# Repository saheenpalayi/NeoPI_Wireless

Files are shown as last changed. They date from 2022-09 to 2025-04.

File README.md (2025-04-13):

# Neoπ Wireless CNC Controller (3-axis) 
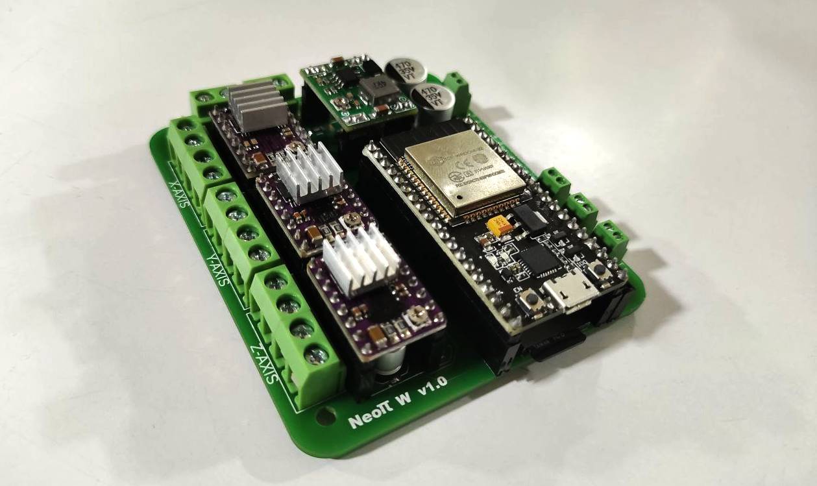
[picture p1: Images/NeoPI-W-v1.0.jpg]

## Project Overview
This project was made for ESP32 based 3-Axis Milling Machines. I started this project During my time at the FAB LAB Kerala for an awesome project Called [FAB Neo](https://fab.cba.mit.edu/classes/865.21/people/rahul/) by Rahul s Rajan. He was developing an Open source fully compact easy to Use PCB Milling Machine Over the years.

## Fetures of Neoπ Wireless CNC Controller
- NodeMCU-32 ESP32 38 Pin  Board based Controller
- SD Card Supported
- A4988/DRV8825 and SPI TMC 2130 stepper Drivers supported
- Reverse Polarity Protection
- Over Voltage protection**
- 12v/24 compatible
- OTA Supports
- PWM Spindle Support
- 2 Probes available (PROB1 and PROB2)
- Power LED Indications RED(power) and Green (5V)

** Optional The board works even without this feature.

## Hardware Pin Mapping

| Sl No | Pin-Names | GPIO |
| --- | --- | --- |
| 1 | X_Dir | GPIO26 |
| 2 | X_Step | GPIO12 |
| 3 | Y_Dir | GPIO25 |
| 4 | Y_Step | GPIO14 |
| 5 | Z_Dir | GPIO33 |
| 6 | Z_Step | GPIO27 |
| 7 | X_limit | GPIO21 |
| 8 | Y_limit | GPIO4 |
| 9 | Z_limit | GPIO15 |
| 10 | Stepper_disable | GPIO13 |
| 11 | Spindle | GPIO17 |
| 12 | PB1 | GPIO32 |
| 13 | PB2 | GPIO22 |

## Firmware

- Use [Grbl_ESP32](https://github.com/bdring/Grbl_Esp32) with [NeoPI_W_v1.h](https://github.com/saheenpalayi/NeoPI_Wireless/blob/main/Firmware/NeoPI_W_v1.h) machine file

## Credits
The Grbl_ESP32 firmware and the ESP32 Hardware is a well-written Open source Project by [bdring](https://github.com/bdring) A K A Barton Dring.

I took reference from these two projects mentioned below
- [Grbl_ESP32_Development_Controller](https://github.com/bdring/Grbl_ESP32_Development_Controller)
- [A 4 axis ESP32 CNC controller for daisy chained SPI stepper drivers](https://github.com/bdring/4_Axis_SPI_CNC#revision-history)
## Revision History
**v1.0**
- version 1 is my first build it has some problems and fixes to do

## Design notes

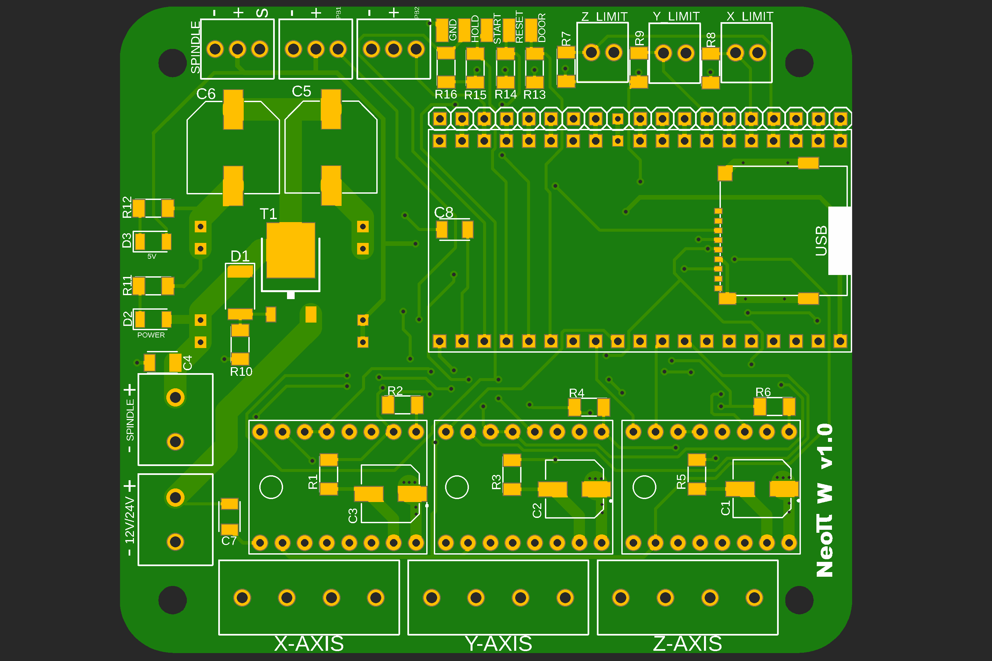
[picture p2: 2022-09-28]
Images/PCB_Top_Side.png

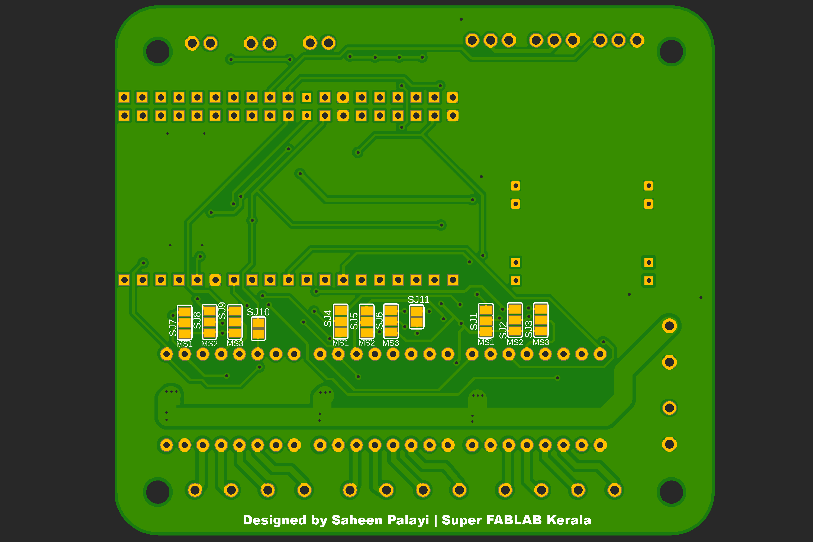
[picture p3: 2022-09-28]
Images/PCB_Bottom_side.png

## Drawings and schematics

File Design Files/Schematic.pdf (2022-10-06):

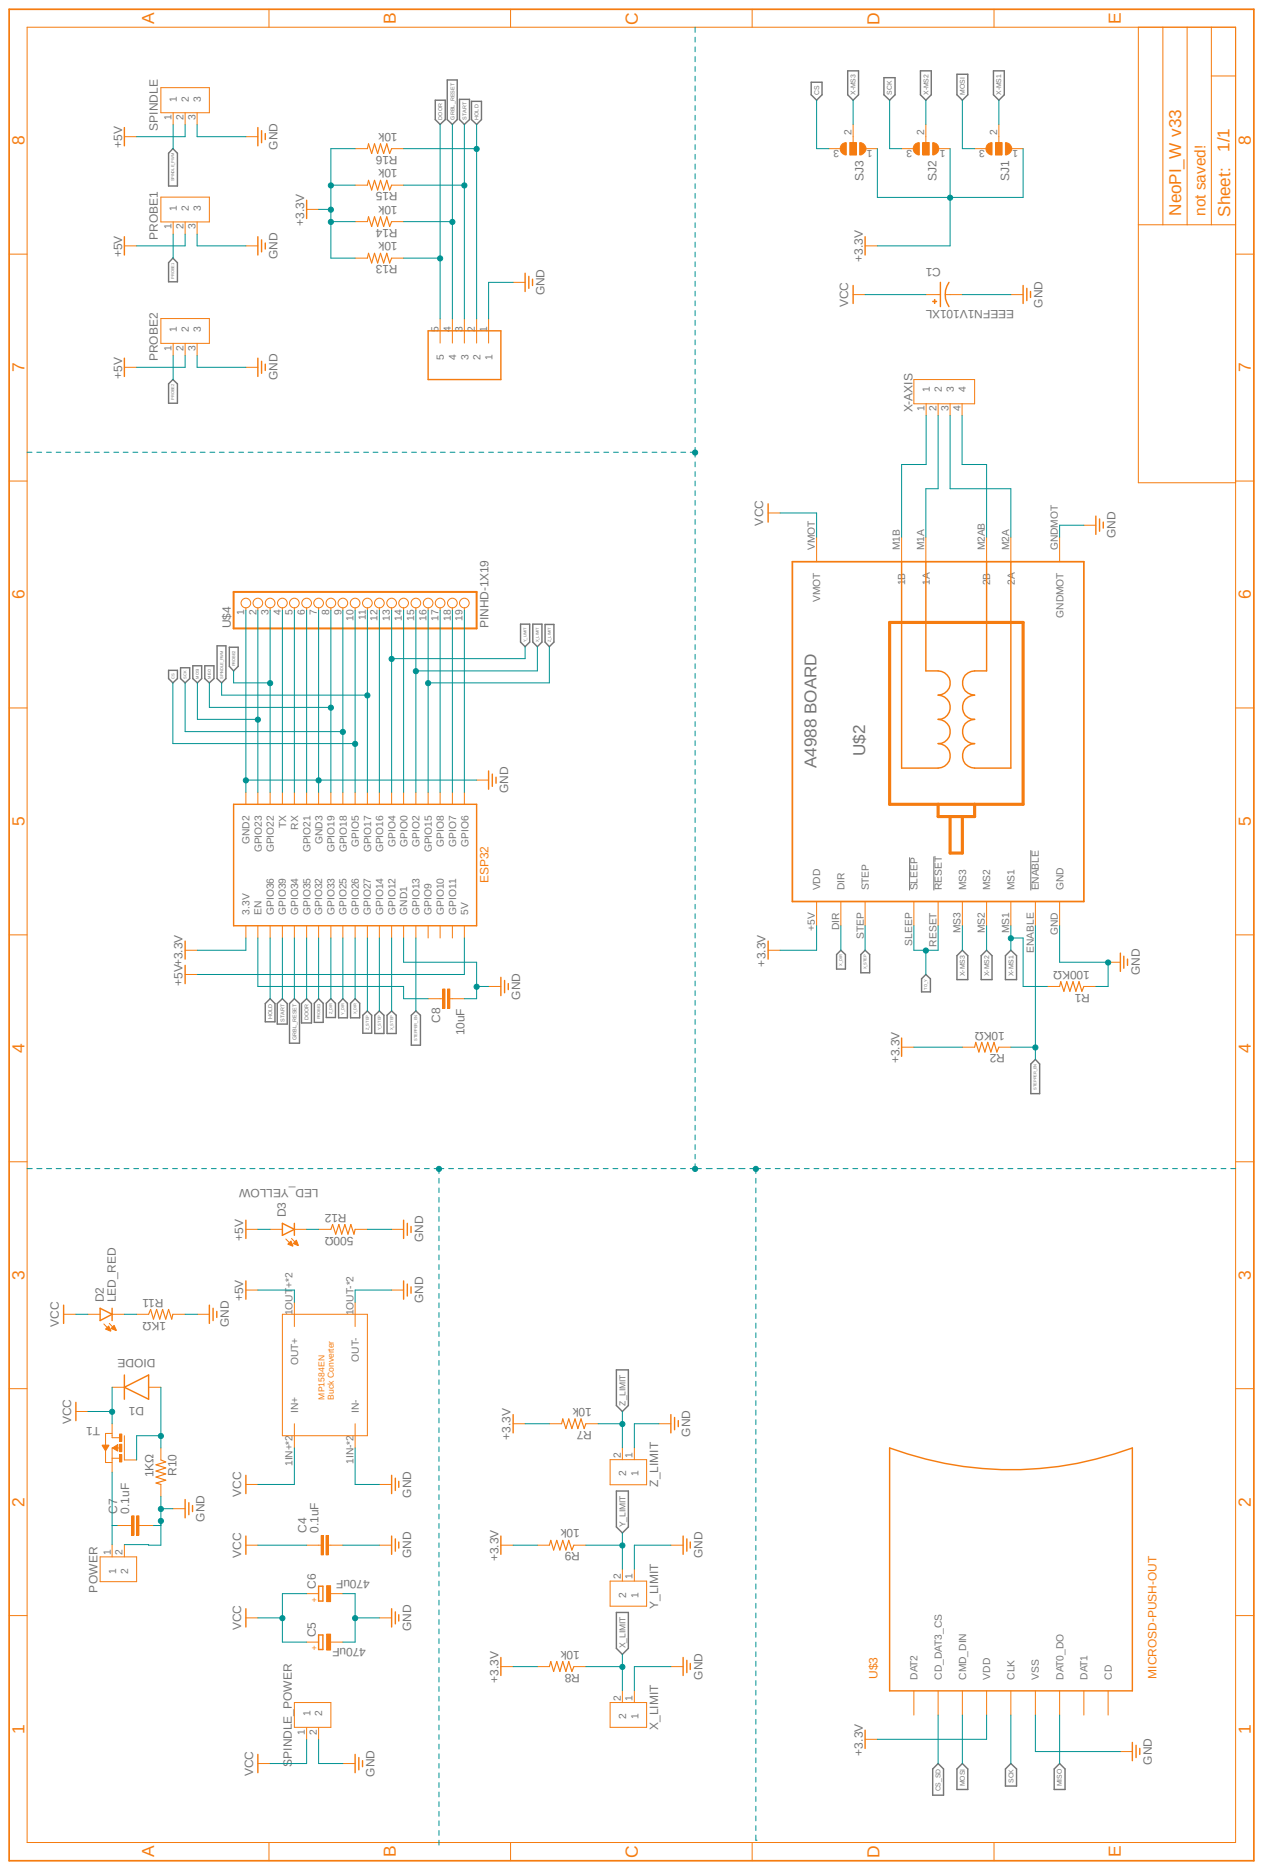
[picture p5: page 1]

C1 IN+ 1IN+*2 IN- 1IN-*2 OUT- 1OUT-*2 OUT+ 1OUT+*2 SPINDLE 1 1 2 2 3 3 X_LIMIT 1 1 2 2 Y_LIMIT 1 1 2 2 Z_LIMIT 1 1 2 2 PROBE1 1 1 2 2 3 3 PROBE2 1 1 2 2 3 3 SPINDLE_POWER 1 1 2 2 POWER 1 1 2 2 C4 R7R8 R9 C5 C6 R10 D1 C7 D2 D3 R11 R12 T1 5 5 4 4 3 3 2 2 1 1 R13 R14 R15 R16 C8 X_STEP X_STEP X_DIR X_DIR TO_Y CS CS SCK SCK SCK MOSI MOSI MOSI MISO MISO CS_SD PROBE2 PROBE2 Z_DIR Z_STEP X-MS3 X-MS3 X-MS2 X-MS2 X-MS1 X-MS1 Y_DIR Y_STEP SPINDLE_PWM SPINDLE_PWM Y_LIMIT Y_LIMIT X_LIMIT X_LIMIT Z_LIMIT Z_LIMIT STEPPER_EN STEPPER_EN PROBE1 PROBE1 HOLD HOLD START START GRBL_RESET GRBL_RESET DOOR DOOR ESP32 U$3 MICROSD-PUSH-OUT MP1584EN Buck Converter ++ NeoPI_W v33 not saved!1/1 Sheet: ABCDE 1 2 3 4 5 6 7 8 ABCDE 1 2 3 4 5 6 7 8

470uF VCC GND GND VCC GND GND GND 1KΩ DIODE0.1uF +5V +5V +5V LED_RED

10k 10k 10k 10k GND +3.3V +3.3V +3.3V10uF 3.3V ENGPIO36 GPIO39 GPIO34 GPIO35 GPIO32 GPIO33 GPIO25 GPIO26 GPIO27 GPIO14 GPIO12 GND1 GPIO13 GPIO9 GPIO10 GPIO11 5V GPIO8 GPIO7 GPIO6 GPIO15 GPIO4 GPIO0 GPIO2 GPIO17 GPIO16 GPIO5 GPIO19 GPIO18 GND3 GPIO21TXRX GPIO23 GPIO22 GND2 U$2 ENABLE ENABLE MS1 MS1 MS2 MS2 MS3 MS3 RESET RESET SLEEP SLEEP STEP STEP DIR DIR VMOT VMOT GNDMOT GNDMOT VDD +5V GND GND 2A M2A 2B M2AB 1A M1A 1B M1B R1 R2 SJ1 3 1 2 SJ2 3 1 2 SJ3 3 1 2 DAT2 CD_DAT3_CS CMD_DIN VDD CLK VSS DAT0_DO DAT1 CD X-AXIS 1 1 2 2 3 3 4 4 U$412345678910111213141516171819

10KΩ +3.3V +3.3V GND +5V+3.3V GND GND PINHD-1X19 VCC

EEEFN1V101XL GND VCC +5V GND GND VCC GND 0.1uF VCC GND

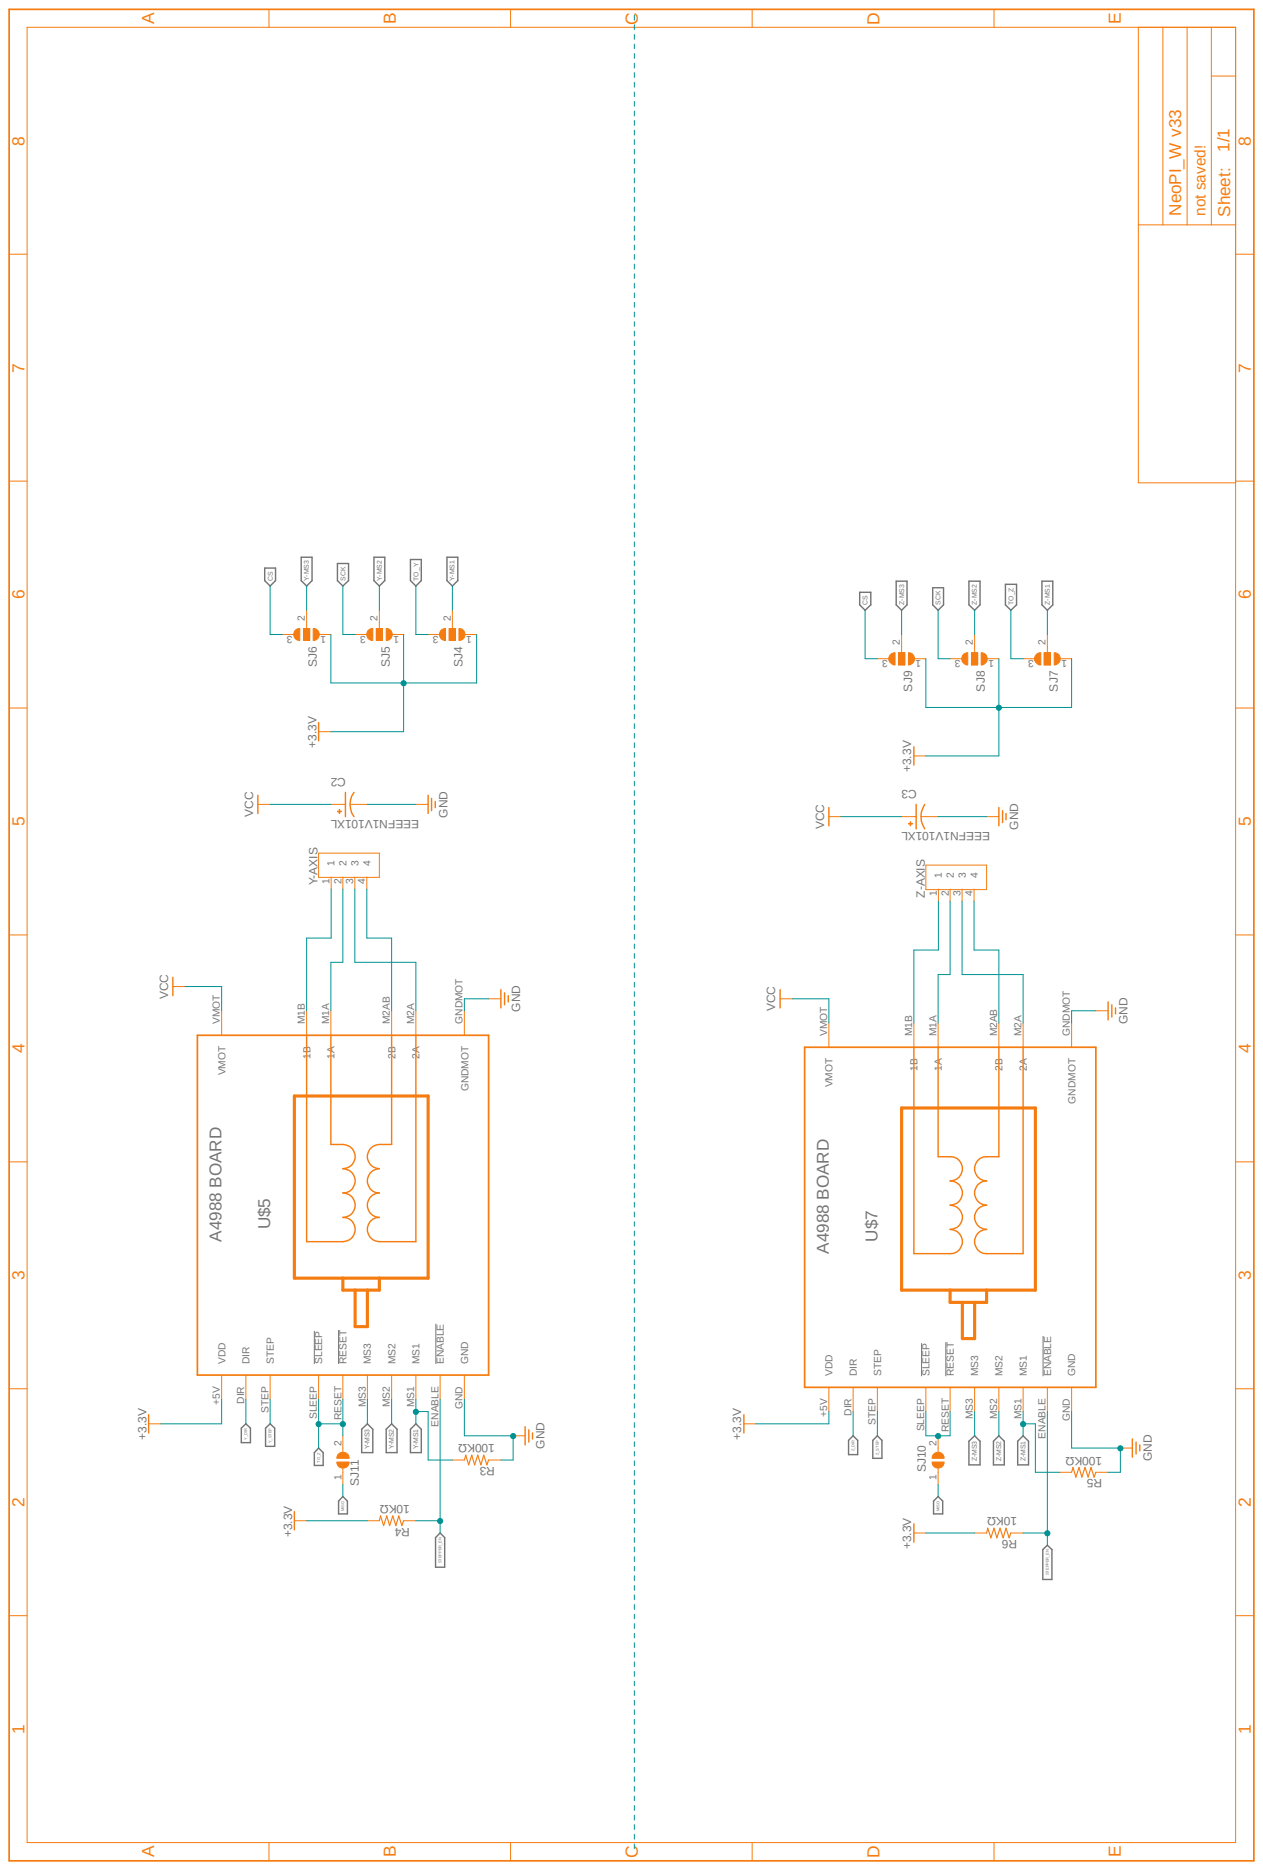
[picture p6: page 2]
10KΩ +3.3V VCC; EEEFN1V101XL GND VCC

C2 C3 SJ102 1SJ11 2 1 CSTO_Y CS SCK SCK MISO MISO TO_Z TO_Z Z_DIR Z_STEP Y-MS3 Y-MS3 Y-MS2 Y-MS2 Y-MS1 Y-MS1 Z-MS3 Z-MS3 Z-MS2 Z-MS2 Z-MS1 Z-MS1 Y_DIR Y_STEP STEPPER_EN STEPPER_EN NeoPI_W v33 not saved!1/1 Sheet: ABCDE 1 2 3 4 5 6 7 8 ABCDE 1 2 3 4 5 6 7 8

EEEFN1V101XL GND +3.3V +3.3V +3.3V +3.3V U$5 ENABLE ENABLE MS1 MS1 MS2 MS2 MS3 MS3 RESET RESET SLEEP SLEEP STEP STEP DIR DIR VMOT VMOT GNDMOT GNDMOT VDD +5V GND GND 2A M2A 2B M2AB 1A M1A 1B M1B R3 R4 SJ4 3 1 2 SJ5 3 1 2 SJ6 3 1 2 Y-AXIS 1 1 2 2 3 3 4 4 U$7 ENABLE ENABLE MS1 MS1 MS2 MS2 MS3 MS3 RESET RESET SLEEP SLEEP STEP STEP DIR DIR VMOT VMOT GNDMOT GNDMOT VDD +5V GND GND 2A M2A 2B M2AB 1A M1A 1B M1B R5 R6 SJ7 3 1 2 SJ8 3 1 2 SJ9 3 1 2 Z-AXIS 1 1 2 2 3 3 4 4

10KΩ +3.3V A4988 BOARD GND GNDVCC

A4988 BOARD GND GNDVCC

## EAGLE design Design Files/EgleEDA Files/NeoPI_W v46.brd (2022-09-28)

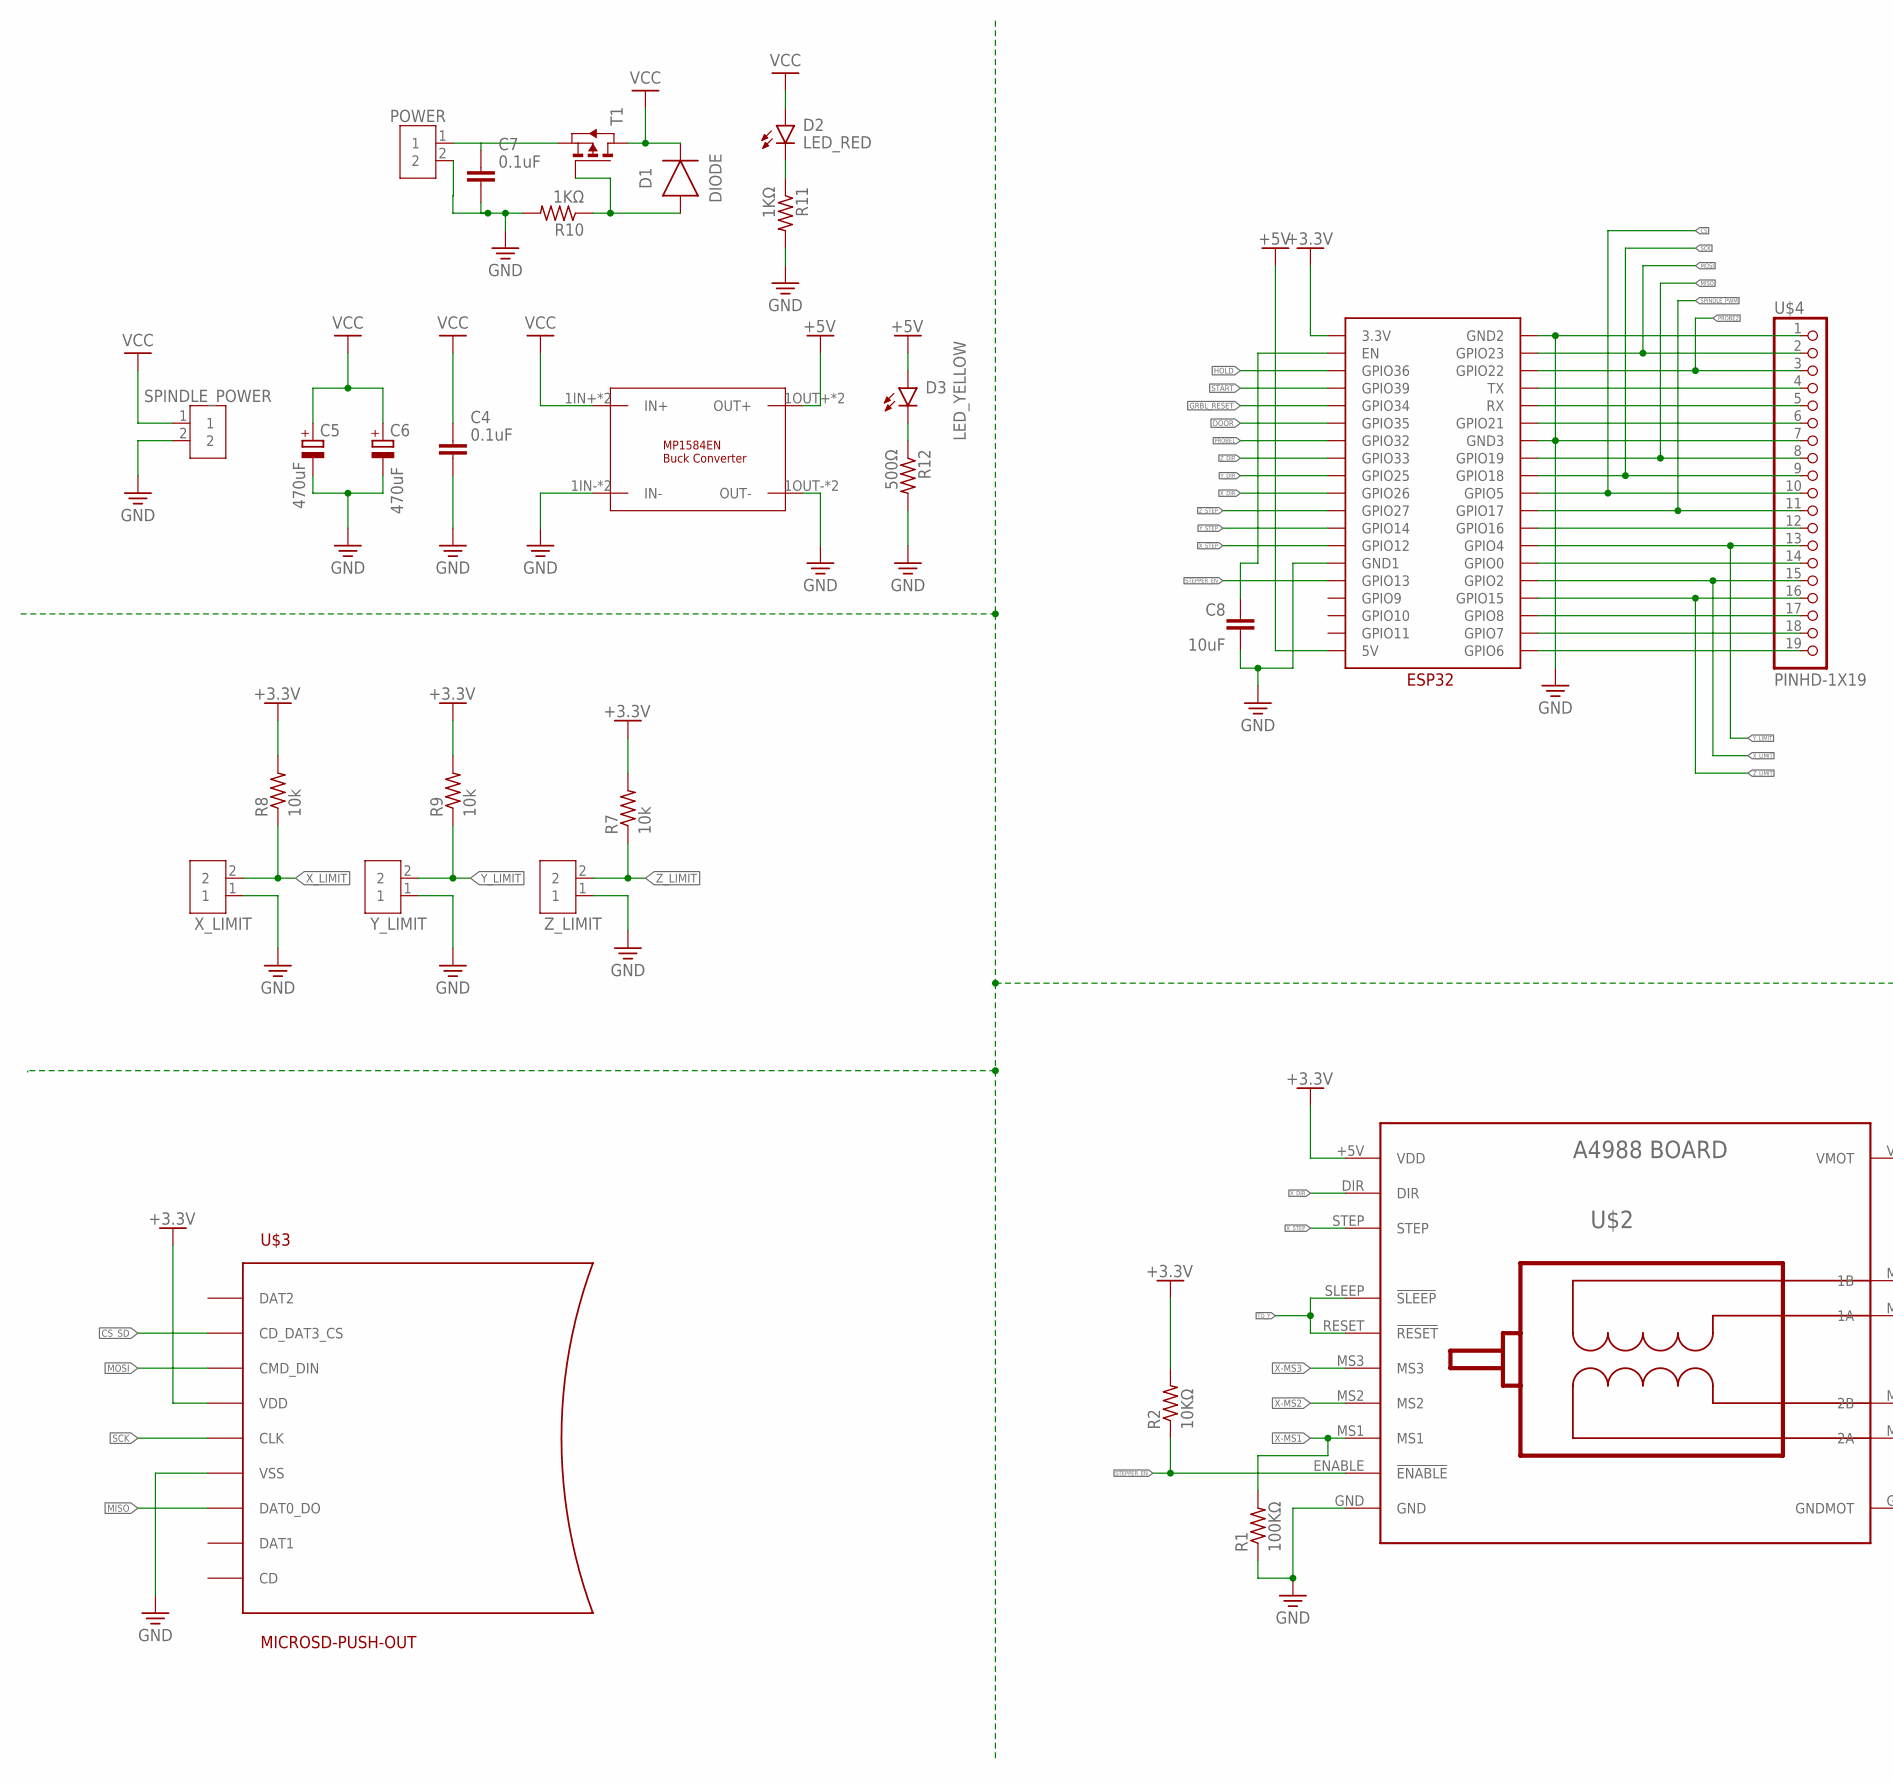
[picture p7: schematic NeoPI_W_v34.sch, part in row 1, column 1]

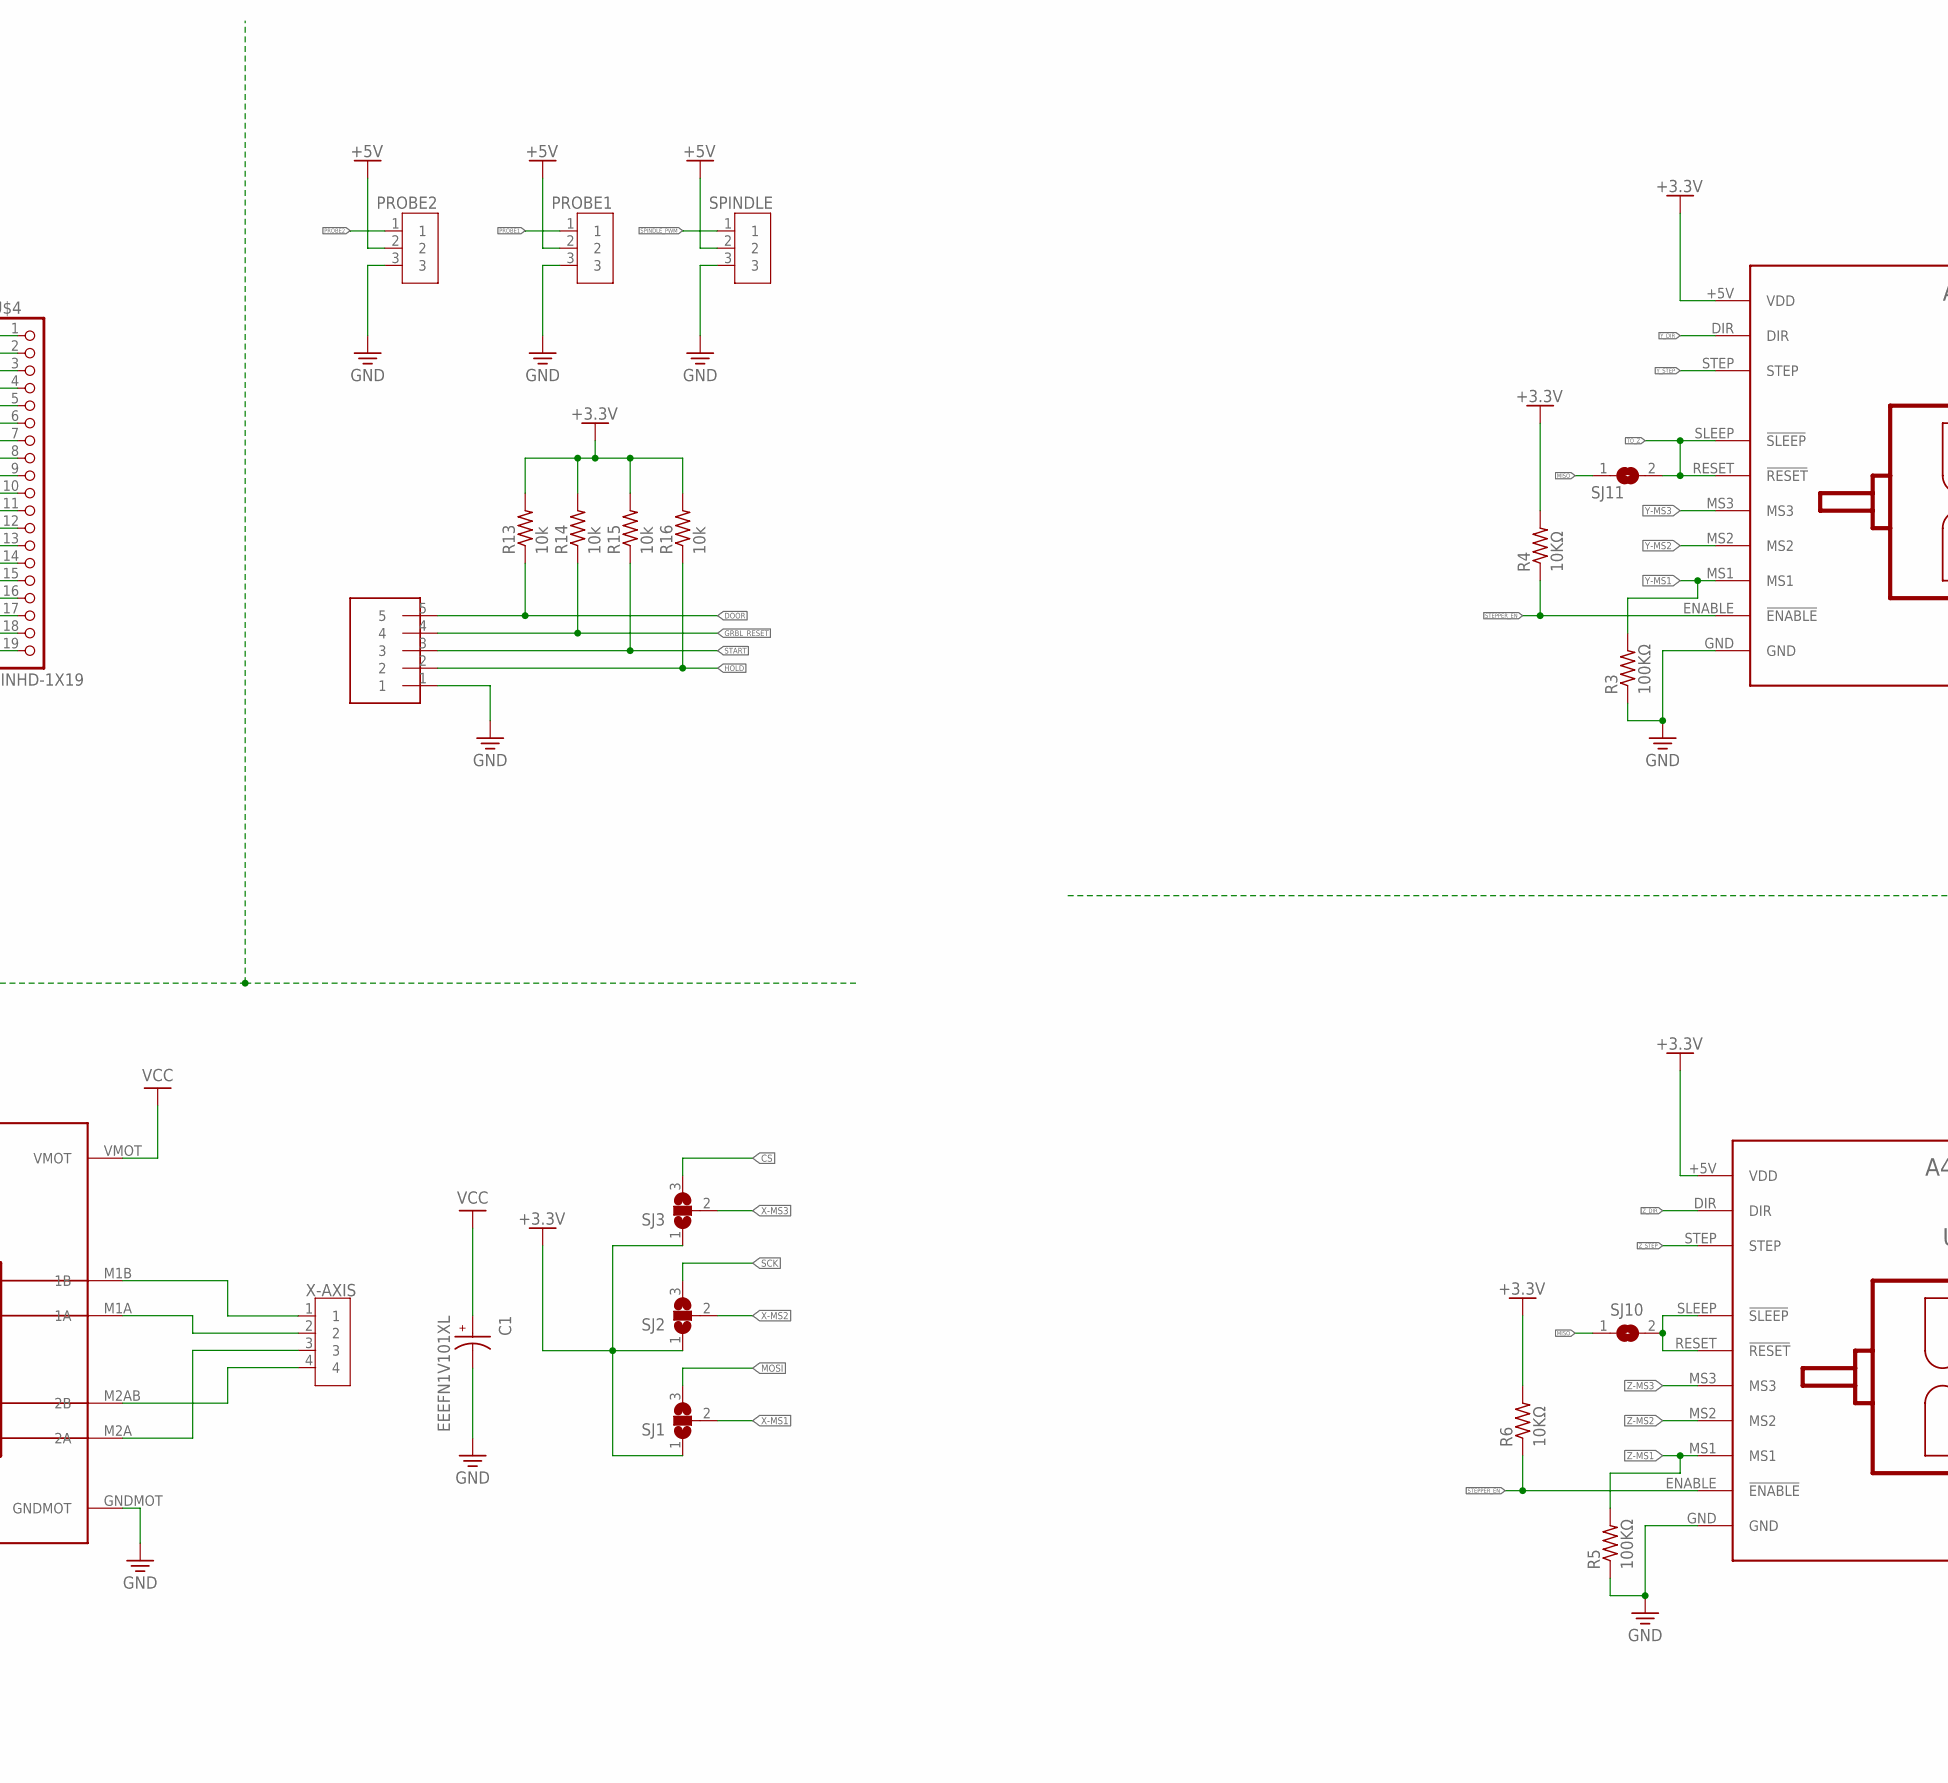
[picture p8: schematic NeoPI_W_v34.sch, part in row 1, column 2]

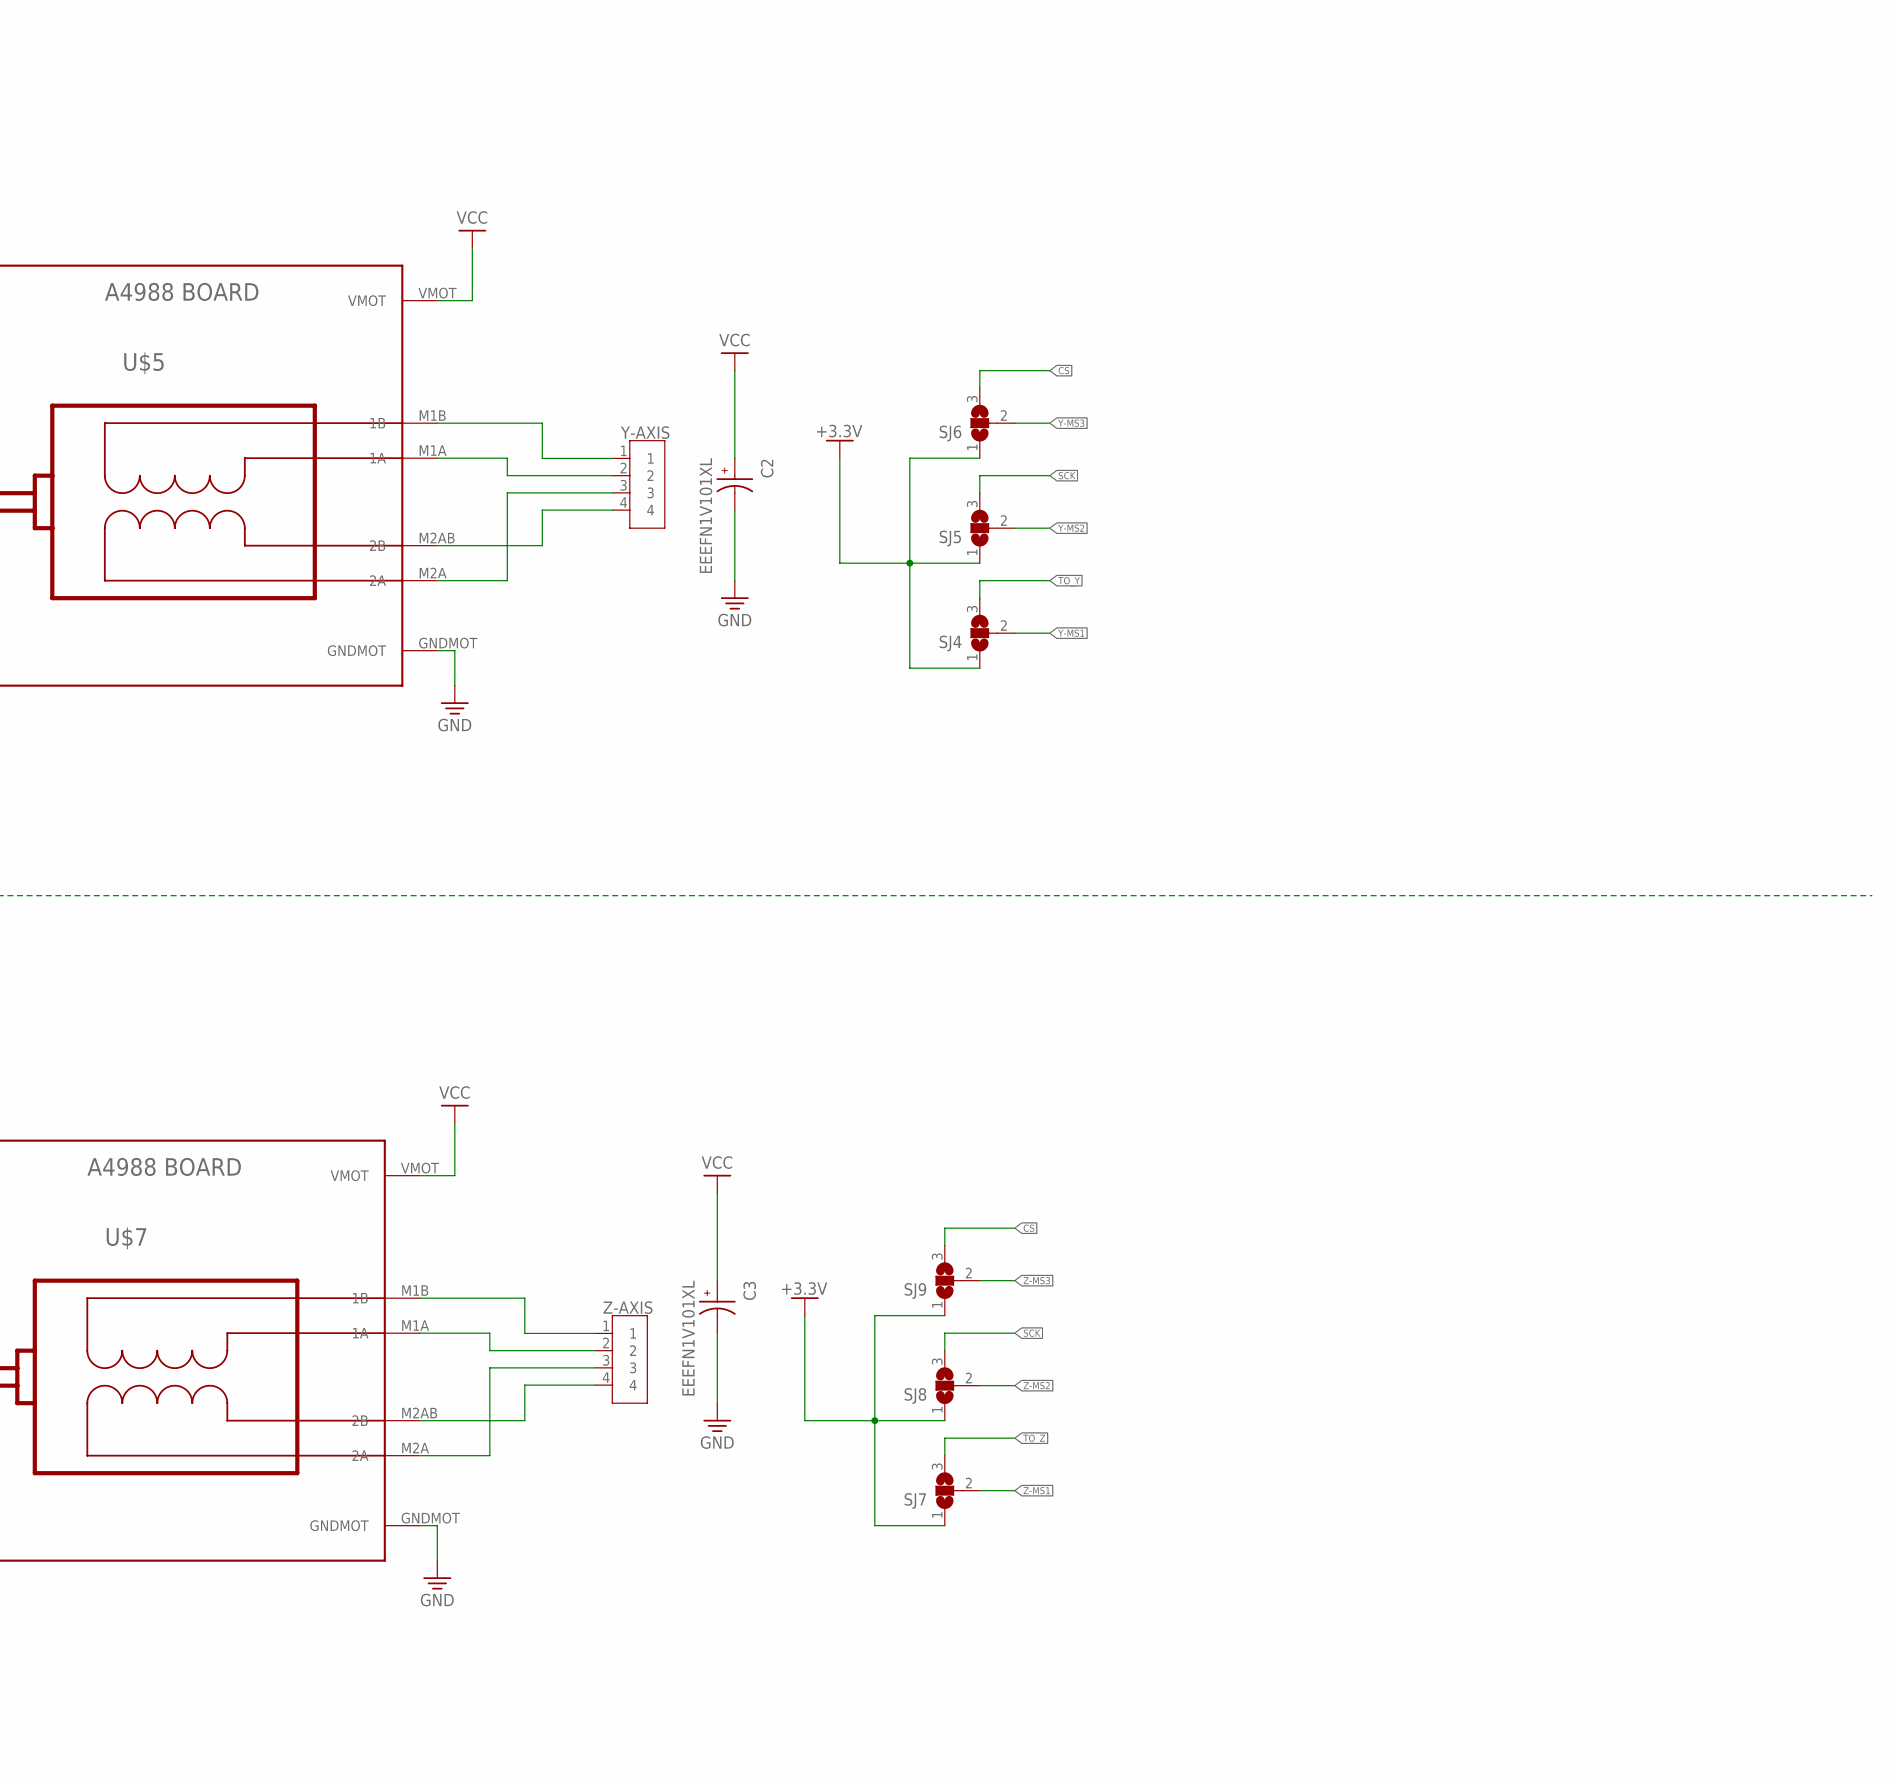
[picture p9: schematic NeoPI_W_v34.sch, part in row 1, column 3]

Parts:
C1, C2, C3: EEEFN1V101XL; CAP_EEEFN1V101XL
C4, C7: 0.1uF; CAPC3216X135
C5, C6: 470uF; CAPAE1030X1050N
C8: 10uF; CAPC3216X135
D1: DIODE; DIOMELF5024
D2: LED_RED; LEDC3216X75N_FLAT-R
D3: LED_YELLOW; LEDC3216X75N_FLAT-Y
POWER: 2828XX-2282837-2; TERMBLK_508-2N
PROBE1, PROBE2: 2828XX-3282834-3; TERMBLK_254-3N
R1, R3, R5: 100KΩ; R1206FAB
R2, R4, R6: 10KΩ; R1206FAB
R7, R8, R9, R13, R14, R15, R16: 10k; R1206FAB
R10, R11: 1KΩ; R1206FAB
R12: 500Ω; R1206FAB
SJ1, SJ2, SJ3, SJ4, SJ5, SJ6, SJ7, SJ8, SJ9: SJ2W; SJ_2
SJ10, SJ11: SJ
SPINDLE: 2828XX-3282834-3; TERMBLK_254-3N
SPINDLE_POWER: 2828XX-2282837-2; TERMBLK_508-2N
T1: PMOSFET; TO252
U$1: ESP32_GRBL
U$2, U$5, U$7: BOARD_A4988
U$3: MICROSD-PUSH-OUT
U$4: PINHD-1X19; 1X19
U$6: MINI-360_DC-TO-DC_BUCK_CONVERTER; MINI_BUCK_CONVERTER
U$8: 1X05_SMD
X-AXIS: 2828XX-4282837-4; TERMBLK_508-4N
X_LIMIT: 2828XX-2282834-2; TERMBLK_254-2N
Y-AXIS: 2828XX-4282837-4; TERMBLK_508-4N
Y_LIMIT: 2828XX-2282834-2; TERMBLK_254-2N
Z-AXIS: 2828XX-4282837-4; TERMBLK_508-4N
Z_LIMIT: 2828XX-2282834-2; TERMBLK_254-2N

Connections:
+3.3V: R2.2, R4.2, R6.2, R7.2, R8.2, R9.2, R13.2, R14.2, R15.2, R16.2, SJ1.1, SJ2.1, SJ3.1, SJ4.1, SJ5.1, SJ6.1, SJ7.1, SJ8.1, SJ9.1, U$1.3.3V, U$2.+5V (VDD), U$3.4 (VDD), U$5.+5V (VDD), U$7.+5V (VDD)
+5V: D3.A, PROBE1.2, PROBE2.2, SPINDLE.2, U$1.5V, U$6.1OUT+ (OUT+), U$6.2OUT+ (OUT+)
CS: SJ3.3, SJ6.3, SJ9.3, U$1.GPIO5, U$4.10
CS_SD: U$3.2 (CD_DAT3_CS)
DOOR: R13.1, U$1.GPIO35, U$8.5
GND: C1.2, C2.2, C3.2, C4.2, C5.2 (-), C6.2 (-), C7.2, C8.2, POWER.2, PROBE1.3, PROBE2.3, R1.1, R3.1, R5.1, R10.2, R11.2, R12.2, SPINDLE.3, SPINDLE_POWER.2, U$1.GND1, U$1.GND2, U$1.GND3, U$2.GND, U$2.GNDMOT, U$3.6 (VSS), U$3.G1 (VSS), U$3.G2 (VSS), U$3.G3 (VSS), U$3.G4 (VSS), U$4.1, U$4.7, U$5.GND, U$5.GNDMOT, U$6.1IN- (IN-), U$6.1OUT- (OUT-), U$6.2IN- (IN-), U$6.2OUT- (OUT-), U$7.GND, U$7.GNDMOT, U$8.1, X_LIMIT.1, Y_LIMIT.1, Z_LIMIT.1
GRBL_RESET: R14.1, U$1.GPIO34, U$8.4
HOLD: R16.1, U$1.GPIO36, U$8.2
MISO: SJ10.1, SJ11.1, U$1.GPIO19, U$3.7 (DAT0_DO), U$4.8
MOSI: SJ1.3, U$1.GPIO23, U$3.3 (CMD_DIN), U$4.2
unnamed: U$2.M1B (1B), X-AXIS.1
unnamed: U$2.M1A (1A), X-AXIS.2
unnamed: U$2.M2A (2A), X-AXIS.3
unnamed: U$2.M2AB (2B), X-AXIS.4
unnamed: U$1.TX, U$4.4
unnamed: D2.C, R11.1
unnamed: U$1.GPIO21, U$4.6
unnamed: U$5.M1B (1B), Y-AXIS.1
unnamed: U$5.M1A (1A), Y-AXIS.2
unnamed: D3.C, R12.1
unnamed: C8.1, U$1.EN
unnamed: U$5.M2A (2A), Y-AXIS.3
unnamed: U$5.M2AB (2B), Y-AXIS.4
unnamed: U$7.M1B (1B), Z-AXIS.1
unnamed: U$7.M1A (1A), Z-AXIS.2
unnamed: SJ10.2, U$7.RESET (!RESET), U$7.SLEEP (!SLEEP)
unnamed: U$7.M2A (2A), Z-AXIS.3
unnamed: U$7.M2AB (2B), Z-AXIS.4
unnamed: U$1.RX, U$4.5
unnamed: U$1.GPIO16, U$4.12
unnamed: C7.1, POWER.1, T1.2 (S)
unnamed: U$1.GPIO0, U$4.14
unnamed: U$1.GPIO8, U$4.17
unnamed: U$1.GPIO7, U$4.18
unnamed: U$1.GPIO6, U$4.19
unnamed: D1.2 (A), R10.1, T1.1 (G)
PROBE1: PROBE1.1, U$1.GPIO32
PROBE2: PROBE2.1, U$1.GPIO22, U$4.3
SCK: SJ2.3, SJ5.3, SJ8.3, U$1.GPIO18, U$3.5 (CLK), U$4.9
SPINDLE_PWM: SPINDLE.1, U$1.GPIO17, U$4.11
START: R15.1, U$1.GPIO39, U$8.3
STEPPER_EN: R2.1, R4.1, R6.1, U$1.GPIO13, U$2.ENABLE (!ENABLE), U$5.ENABLE (!ENABLE), U$7.ENABLE (!ENABLE)
TO_Y: SJ4.3, U$2.RESET (!RESET), U$2.SLEEP (!SLEEP)
TO_Z: SJ7.3, SJ11.2, U$5.RESET (!RESET), U$5.SLEEP (!SLEEP)
VCC: C1.1, C2.1, C3.1, C4.1, C5.1 (+), C6.1 (+), D1.1 (C), D2.A, SPINDLE_POWER.1, T1.3 (D), U$2.VMOT, U$5.VMOT, U$6.1IN+ (IN+), U$6.2IN+ (IN+), U$7.VMOT
X-MS1: R1.2, SJ1.2, U$2.MS1
X-MS2: SJ2.2, U$2.MS2
X-MS3: SJ3.2, U$2.MS3
X_DIR: U$1.GPIO26, U$2.DIR
X_LIMIT: R8.1, U$1.GPIO2, U$4.15, X_LIMIT.2
X_STEP: U$1.GPIO12, U$2.STEP
Y-MS1: R3.2, SJ4.2, U$5.MS1
Y-MS2: SJ5.2, U$5.MS2
Y-MS3: SJ6.2, U$5.MS3
Y_DIR: U$1.GPIO25, U$5.DIR
Y_LIMIT: R9.1, U$1.GPIO4, U$4.13, Y_LIMIT.2
Y_STEP: U$1.GPIO14, U$5.STEP
Z-MS1: R5.2, SJ7.2, U$7.MS1
Z-MS2: SJ8.2, U$7.MS2
Z-MS3: SJ9.2, U$7.MS3
Z_DIR: U$1.GPIO33, U$7.DIR
Z_LIMIT: R7.1, U$1.GPIO15, U$4.16, Z_LIMIT.2
Z_STEP: U$1.GPIO27, U$7.STEP

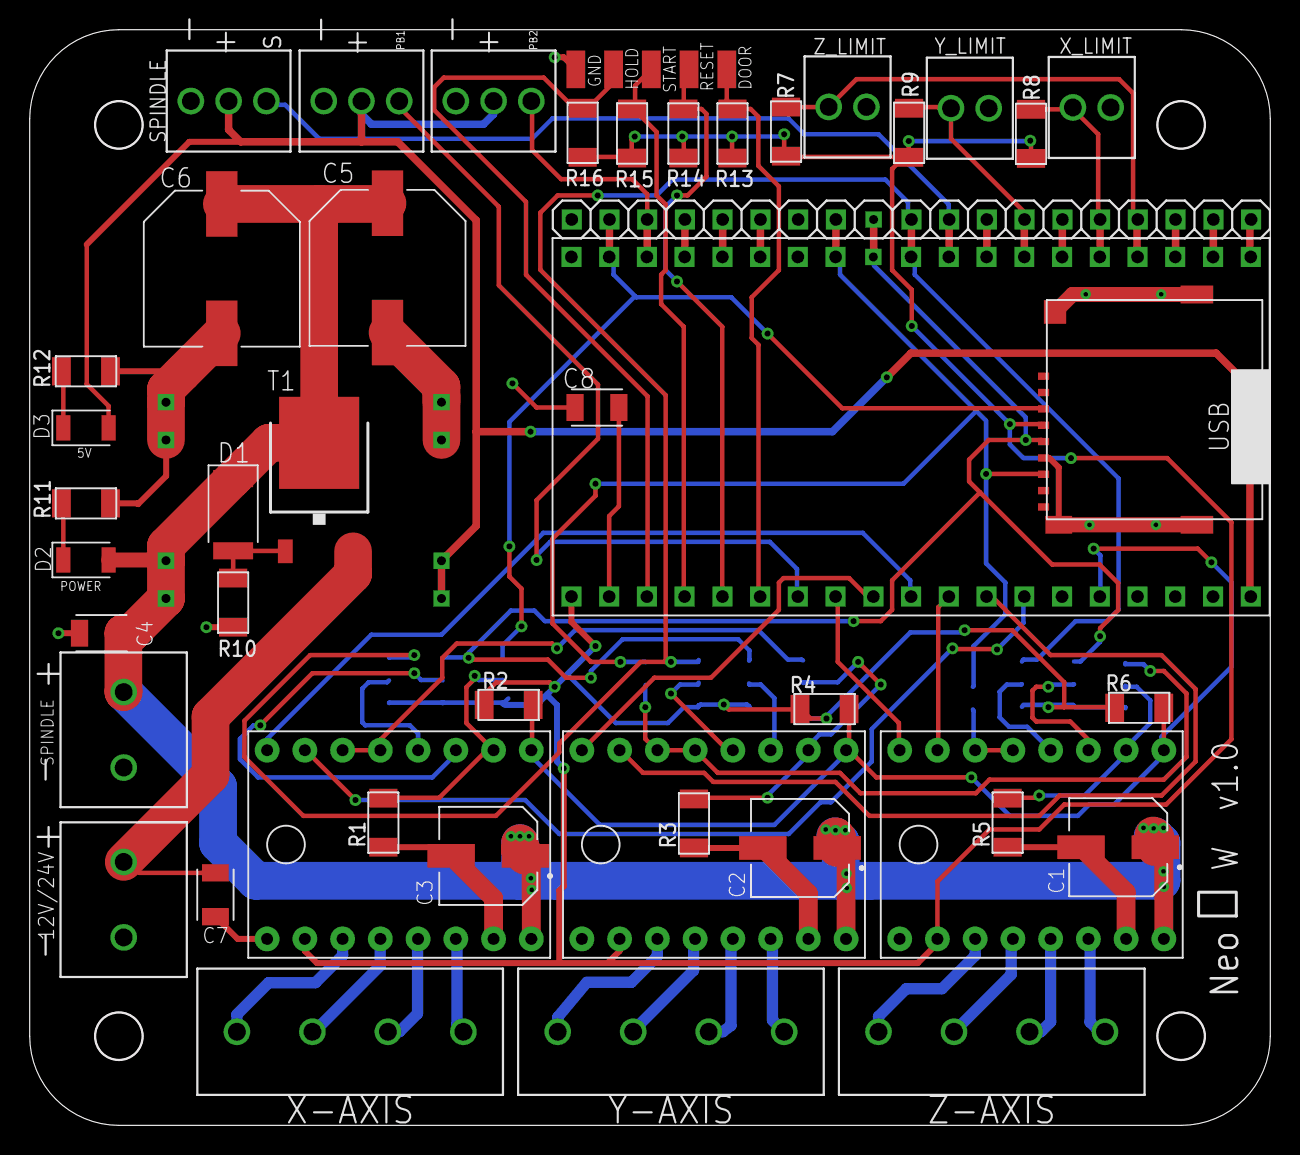
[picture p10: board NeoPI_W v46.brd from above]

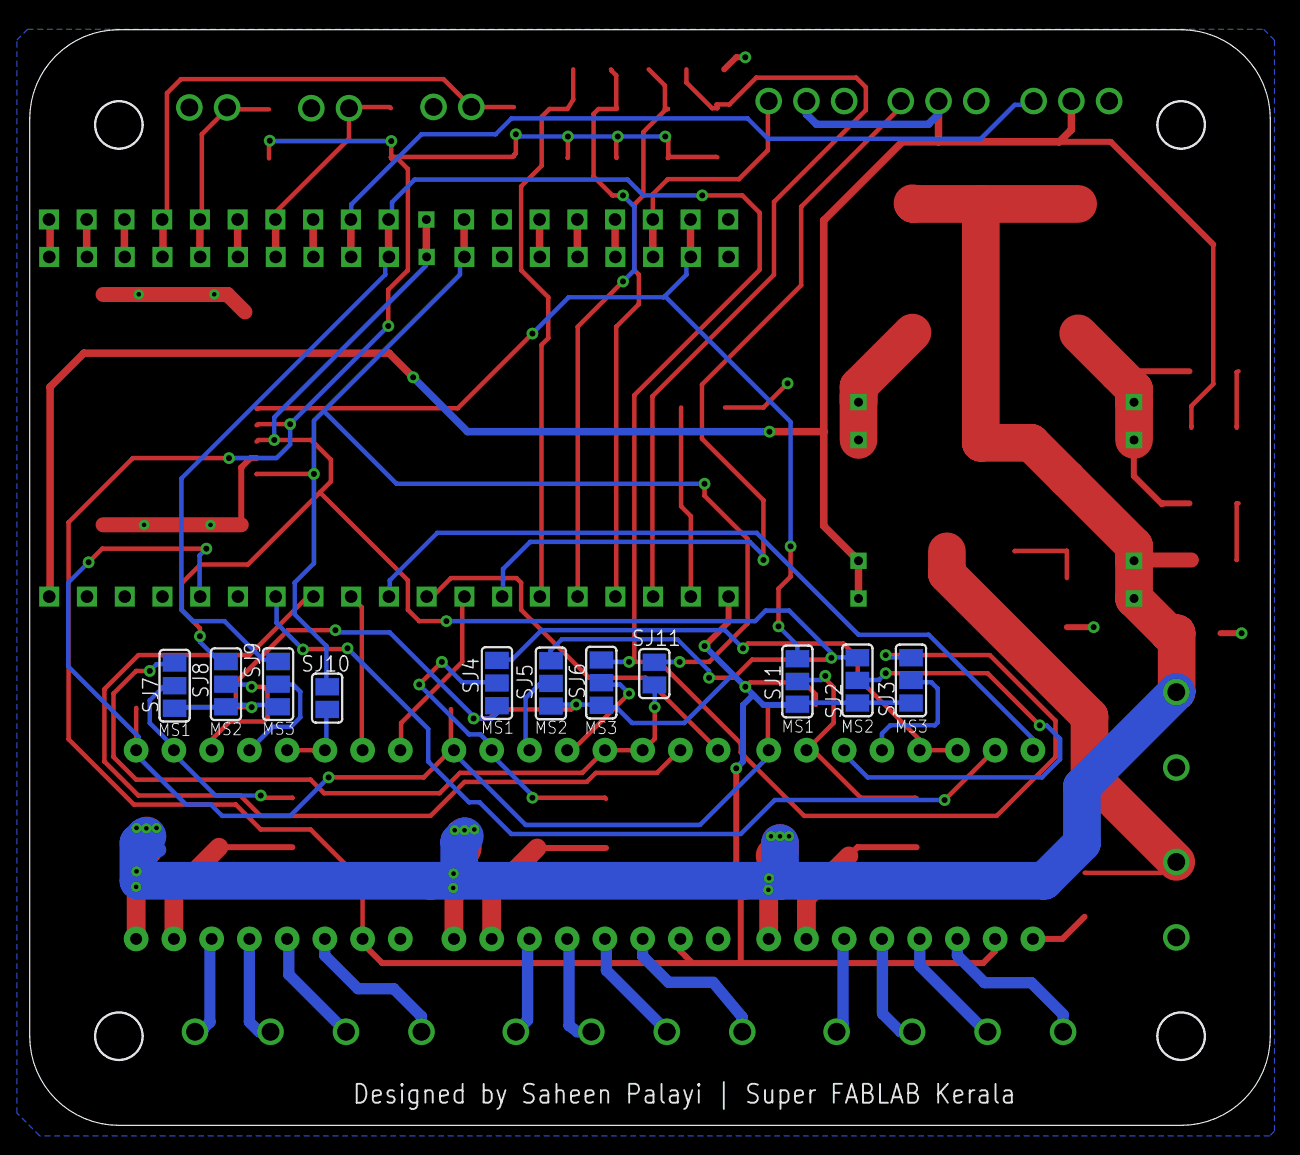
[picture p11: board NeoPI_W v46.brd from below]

Board: 2 copper layers, 83.5 x 73.7 mm, 58 parts (11 on the bottom side), 62 nets.

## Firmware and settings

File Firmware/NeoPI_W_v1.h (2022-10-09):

#pragma once
// clang-format off

/*
    NeoPI_W_v1.h
    Part of Grbl_ESP32

    Pin assignments for the NeoPI Wireless CNC Controller(3-axis), v1.0 and later.
    https://github.com/saheenpalayi/NeoPI_Wireless

    2018    - Bart Dring
    2020    - Mitch Bradley
    2022    - Saheen Palayi

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
    You should have received a copy of the GNU General Public License
    along with Grbl_ESP32.  If not, see <http://www.gnu.org/licenses/>.
*/

#define MACHINE_NAME            "NeoPI_W_v1"

#define X_STEP_PIN              GPIO_NUM_12
#define X_DIRECTION_PIN         GPIO_NUM_26
#define Y_STEP_PIN              GPIO_NUM_14
#define Y_DIRECTION_PIN         GPIO_NUM_25
#define Z_STEP_PIN              GPIO_NUM_27
#define Z_DIRECTION_PIN         GPIO_NUM_33

#define X_LIMIT_PIN             GPIO_NUM_2
#define Y_LIMIT_PIN             GPIO_NUM_4
#define Z_LIMIT_PIN             GPIO_NUM_15


// OK to comment out to use pin for other features
#define STEPPERS_DISABLE_PIN    GPIO_NUM_13

#define SPINDLE_TYPE            SpindleType::BESC
#define SPINDLE_OUTPUT_PIN      GPIO_NUM_17   // labeled SpinPWM
// #define SPINDLE_ENABLE_PIN      GPIO_NUM_22  // labeled SpinEnbl

// #define COOLANT_MIST_PIN        GPIO_NUM_21  // labeled Mist
// #define COOLANT_FLOOD_PIN       GPIO_NUM_25  // labeled Flood
#define PROBE_PIN               GPIO_NUM_32  // labeled Probe


/*
#define CONTROL_SAFETY_DOOR_PIN GPIO_NUM_35  // labeled Door,  needs external pullup
#define CONTROL_RESET_PIN       GPIO_NUM_34  // labeled Reset, needs external pullup
#define CONTROL_FEED_HOLD_PIN   GPIO_NUM_36  // labeled Hold,  needs external pullup
#define CONTROL_CYCLE_START_PIN GPIO_NUM_39  // labeled Start, needs external pullup
*/

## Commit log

2022-10-06 Readme update and fixes
    Fixed some issues in schematic
    [ENeoPI-Wireless_v31.sch, NeoPI-Wireless v44.brd, NeoPI_W v46.brd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]
2022-10-09 doc-updates
    firmware folder added with .h file
    image of fully assembled PCB Added
2025-04-13 added pin mapping table
2025-04-21 firmware added for velichapad
    [alarm_codes_en_US.csv, build_option_codes_en_US.csv, error_codes_en_US.csv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]

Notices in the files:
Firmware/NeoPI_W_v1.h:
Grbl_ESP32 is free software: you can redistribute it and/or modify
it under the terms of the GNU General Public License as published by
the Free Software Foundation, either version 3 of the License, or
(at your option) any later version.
